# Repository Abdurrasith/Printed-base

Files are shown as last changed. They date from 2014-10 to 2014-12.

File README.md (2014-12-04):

# Robopoly demonstration robot 3D printed base

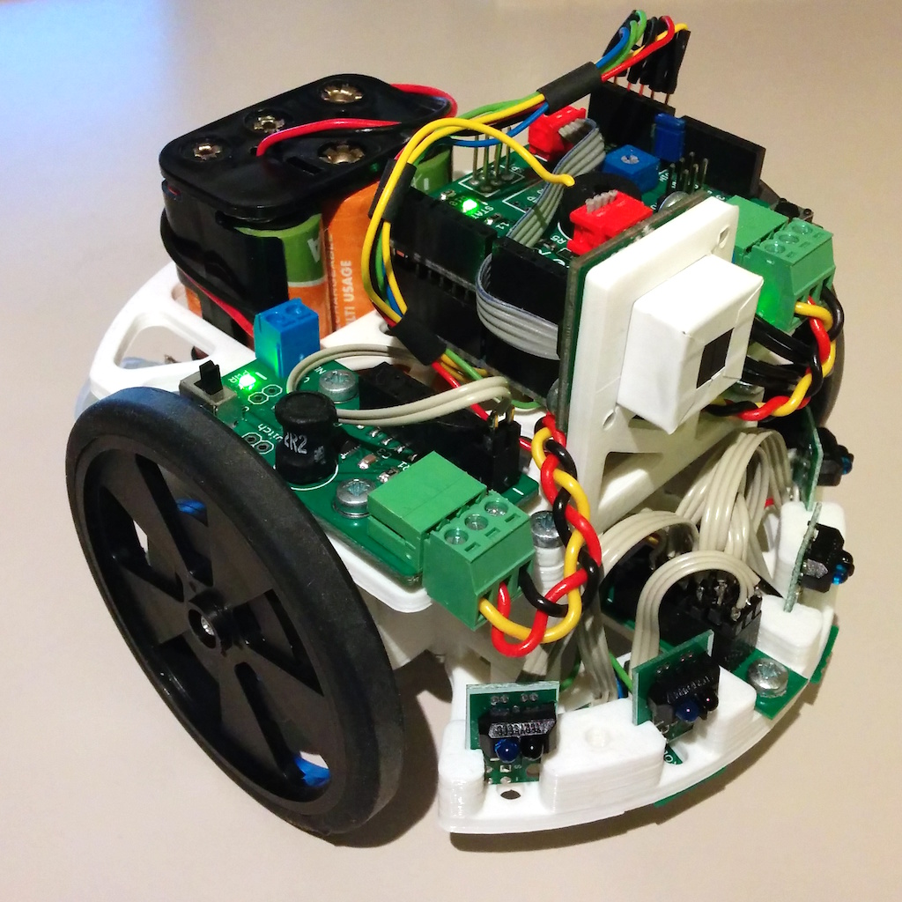
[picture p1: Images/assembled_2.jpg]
Demonstration robot front

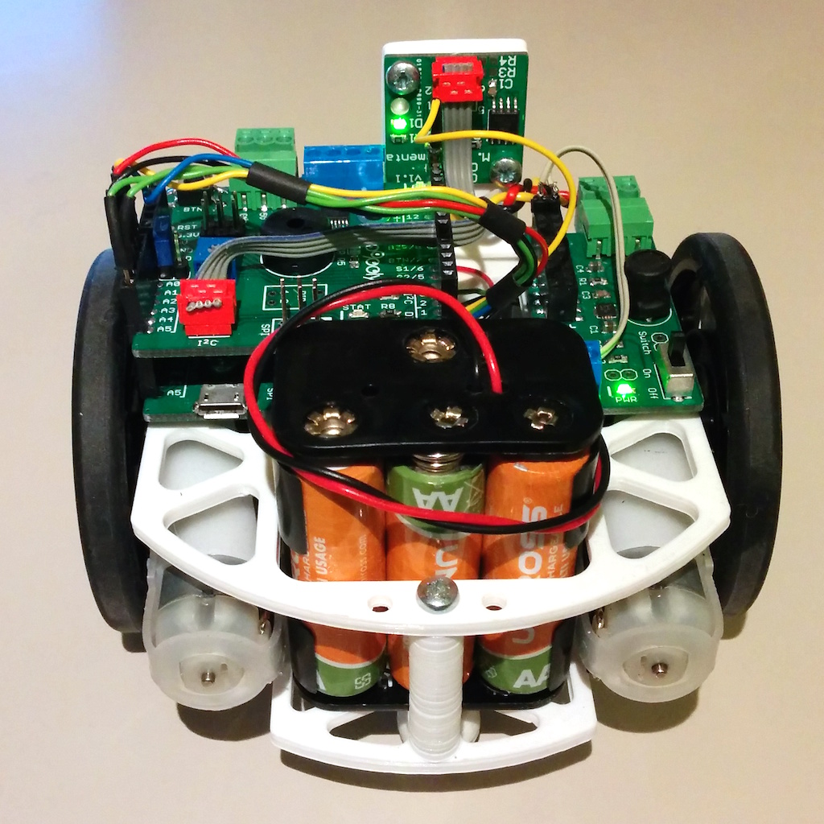
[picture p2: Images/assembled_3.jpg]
Demonstration robot back

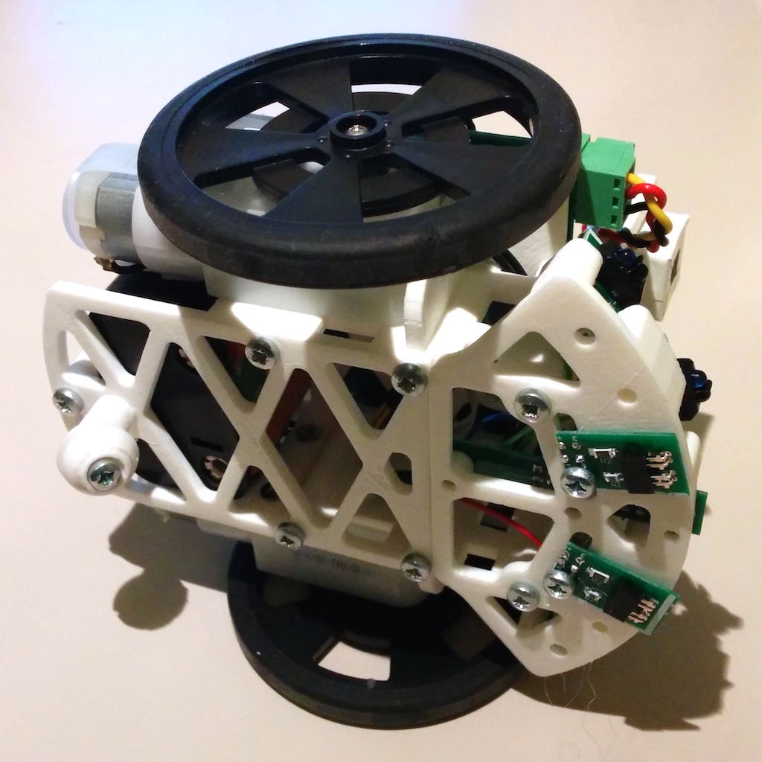
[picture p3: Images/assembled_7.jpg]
Printed caster wheel


The Robopoly demonstration robot is intended to serve as a modular base for demonstrations during [Robopoly lectures](http://robopoly.epfl.ch/demons) to show off the robotics platform capabilities. It is modular, all important parts are accessible, has a small footprint and is made only using electronics from the [kit PRisme](http://robopoly.epfl.ch/prisme).

## Design

Since the parts are intended to be printed with a 3D printer with fused filament fabrication (FFF) method they are small and full of holes in order to avoid warp because of uneven material cooling on 3D printers lacking a heated bed and using excessive amounts of material.

The front of the robot can accomodate different modules depending on the task at hand. 4 holes for M3 screws can be used to attach a custom add-on.

The center of the platform is empty, that space can be used to route electrical wires from the front of the robot to the [PRismino](https://github.com/Robopoly/PRismino) or store some additional electronics.

The USB port is easely accessible for programming and all the electronics are on top of the robot allowing easy access.

Horizontal holes in the supports are square because when printing big horizontal round holes with FFF method the plastic tends to warp upwards when the hole is being closed at the top because of unequal cooling, this basically creates an obstacle for the extruder which is to be avoided at all costs, square holes do not warp.

## Parts list

| Part | Quantity |
| --- | --- |
| Base | 1 |
| Top | 1 |
| Support left | 1 |
| Support right | 1 |
| Support rear | 1 |
| Caster roller | 1 |
| Caster wheel | 1 |
| Front | 1 |
| Linear camera support | 1 |
| M3x8 countersunk head screw for motors | 4 |
| M3x5 pan head screw for rear support | 2 |
| M3x8 pan head screw for electronics, rear support and caster roller | 5 |
| M3x10 countersunk head screw for caster wheel | 1 |
| M3x10 pan head screw for the frame | 10 |
| M3 washer for caster roller | 1 |

When assembling start with the motors as the holes won't be accessible with a screwdriver later on.

## Robopoly Control Center

The plaform is suited to be used with [Robopoly Control Center](https://github.com/Robopoly/RobopolyControlCenter), a [Google Chrome add-on](https://chrome.google.com/webstore/detail/robopoly-control-center/kimabfnmacaikklmibbbomomjffkfalo) that can remotely control the mobile platform, make it do some tasks and report pin values over USB or Bluetooth.

## Licence

The Robopoly demonstration robot printed base is published under [Creative Commons Attribution license](http://creativecommons.org/licenses/by/3.0/).



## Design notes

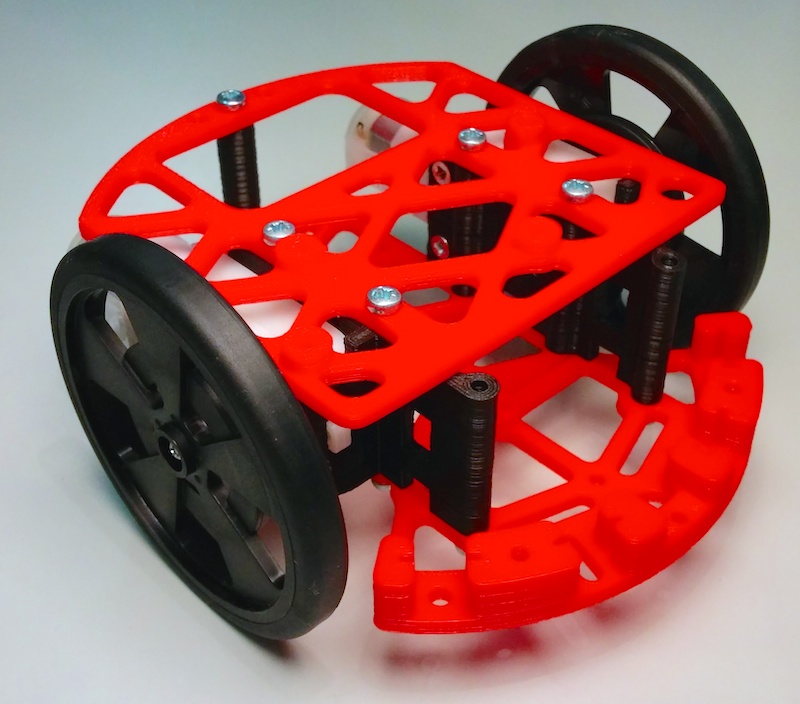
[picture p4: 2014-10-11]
Images/demo_1.jpg

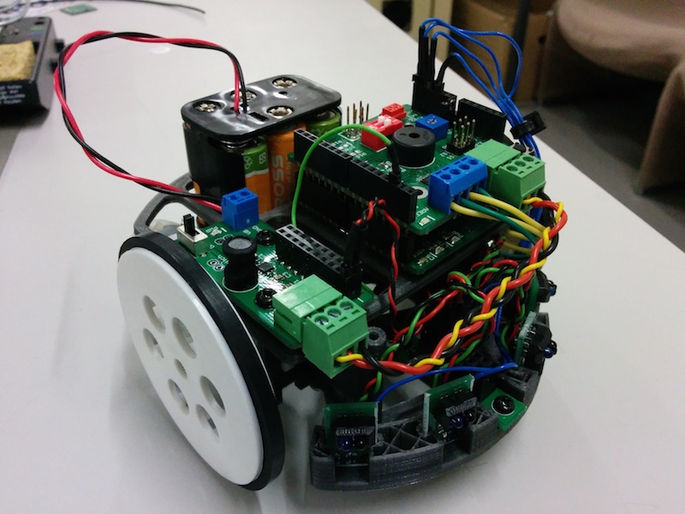
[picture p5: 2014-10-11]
Images/prototype.jpg

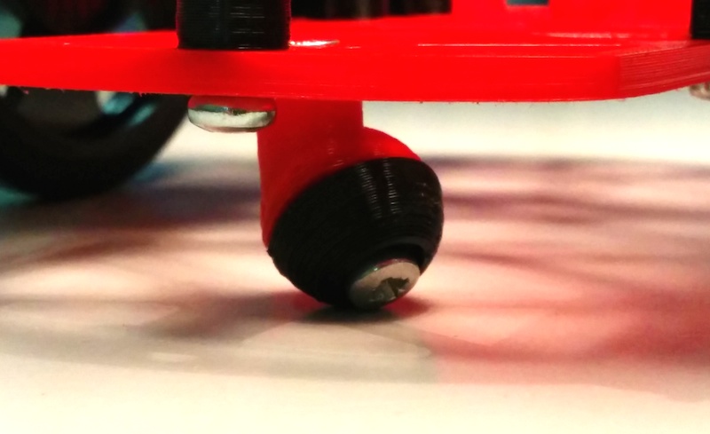
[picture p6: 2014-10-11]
Images/demo_3.jpg

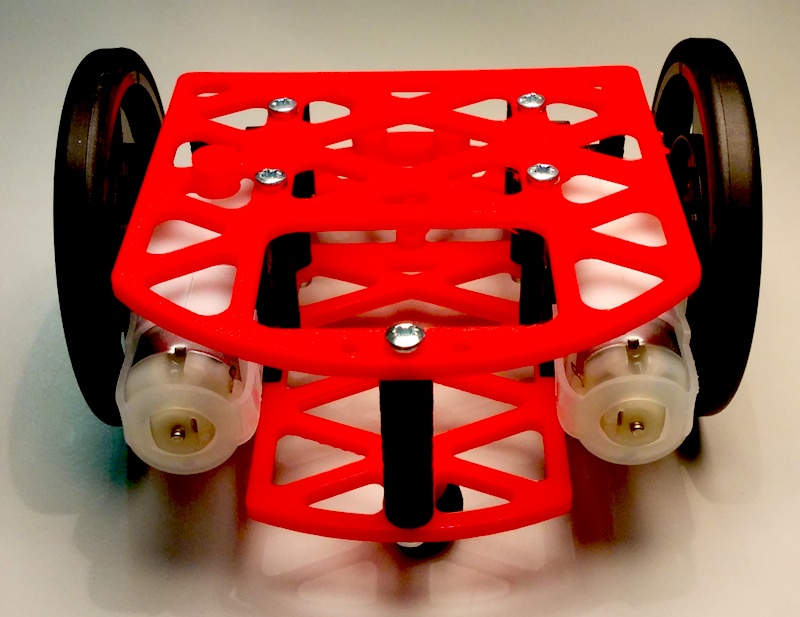
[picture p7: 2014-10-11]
Images/demo_2.jpg

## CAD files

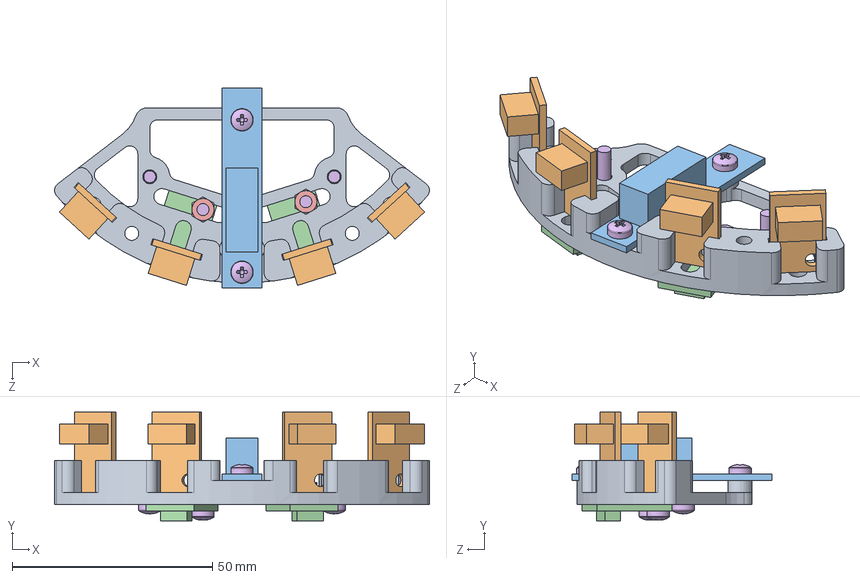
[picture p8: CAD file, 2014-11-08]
SolidWorks files/front_assembly.SLDASM
93.5 x 27.1 x 50.0 mm
front
ir_tcrt5000 x 4
rack
ir_tcrt1000 x 2
hex nut style 1 gradeab_iso x 2
pan head cross recess screw_iso x 6

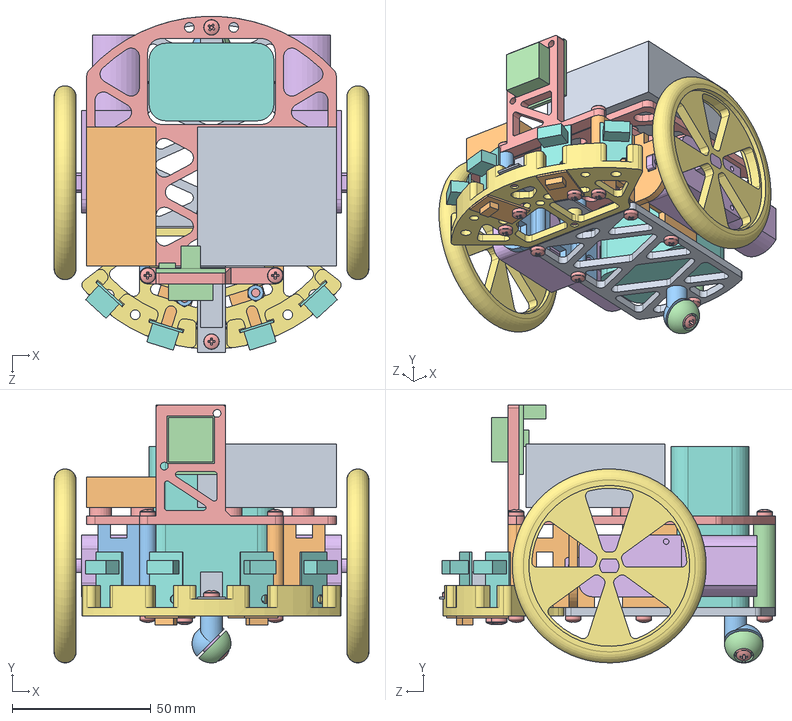
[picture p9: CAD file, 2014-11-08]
SolidWorks files/assembly.SLDASM
113.6 x 93.0 x 121.3 mm
base
support_left
support_right
support_rear
top
motor x 2
wheel x 2
battery_pack
prismino
power
caster_wheel
caster_roller
pan head cross recess screw_iso x 23
plain washer 10669 type nl_iso
front
ir_tcrt5000 x 4
rack
ir_tcrt1000 x 2
hex nut style 1 gradeab_iso x 2
linear_camera
support_linear_camera
countersunk flat head cross recess screw_iso x 5

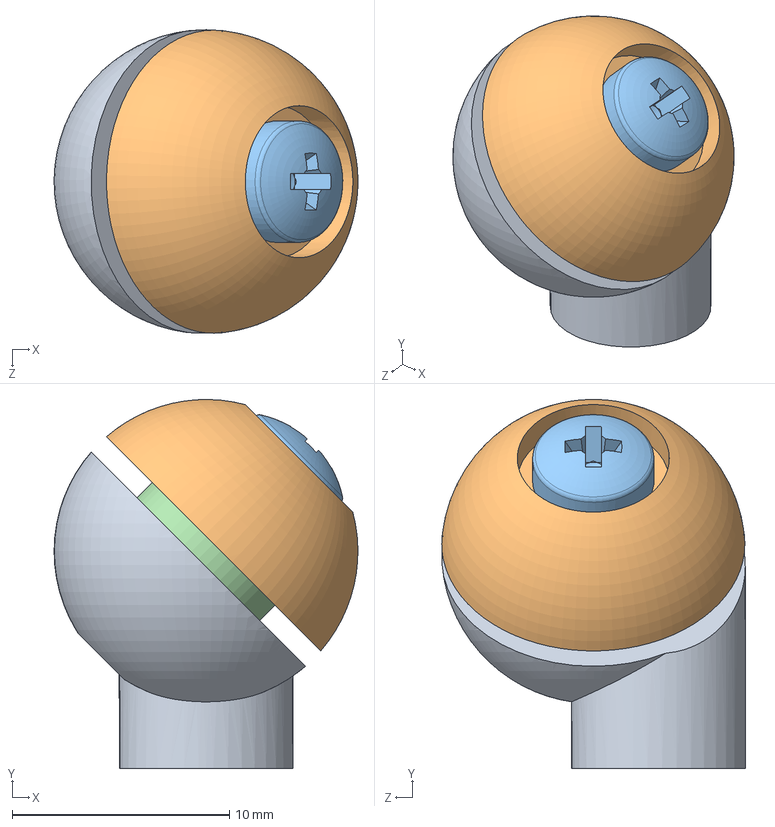
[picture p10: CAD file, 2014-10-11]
SolidWorks files/caster_assembly.SLDASM
14.0 x 17.0 x 14.0 mm
caster_wheel
caster_roller
pan head cross recess screw_iso
plain washer 10669 type nl_iso

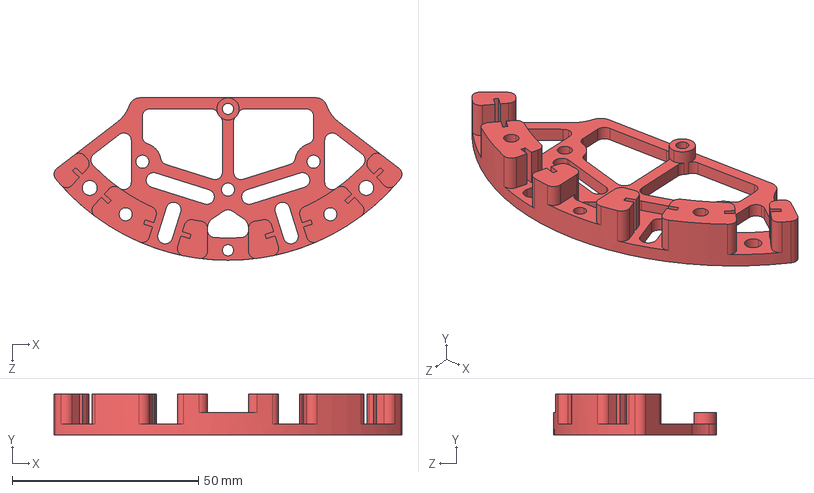
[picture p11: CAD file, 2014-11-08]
STEP files/front.STEP
93.5 x 11.0 x 43.7 mm

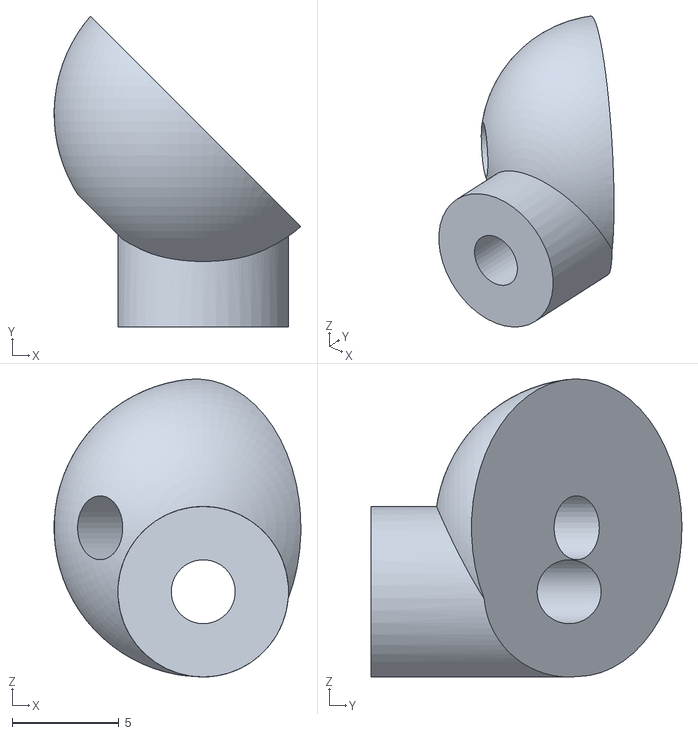
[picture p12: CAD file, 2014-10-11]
STL files/caster_base.STL
11.6 x 14.6 x 14.0

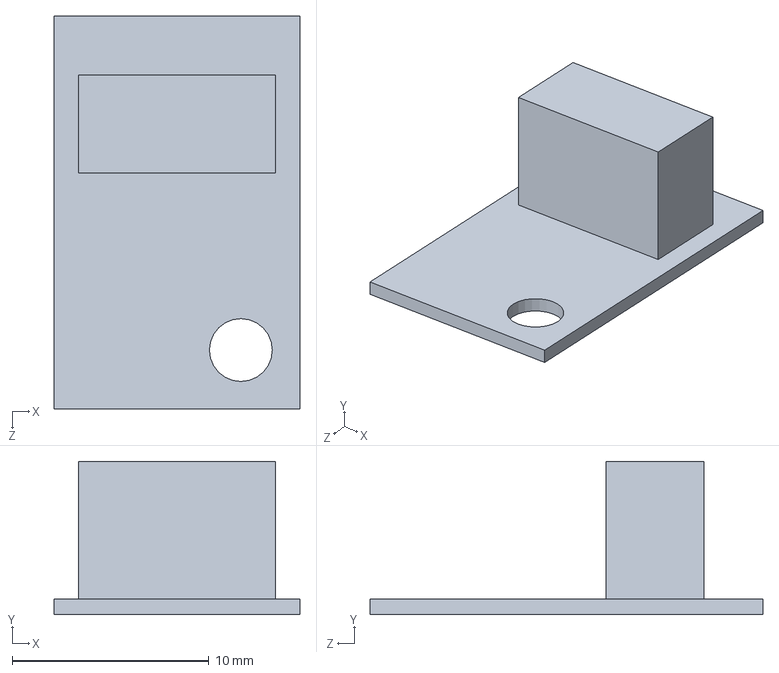
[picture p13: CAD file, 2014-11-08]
SolidWorks files/ir_tcrt5000.SLDPRT
12.5 x 7.80 x 20.0 mm

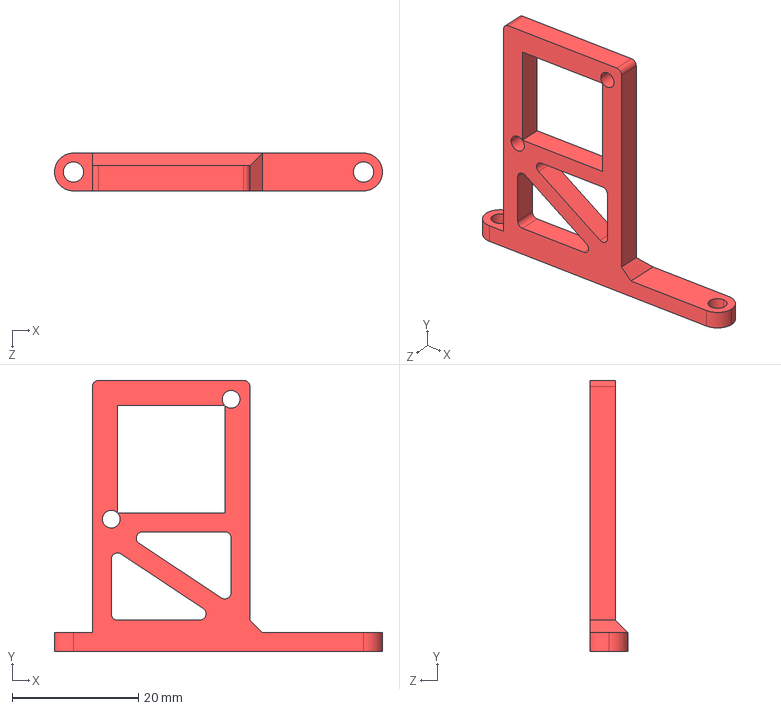
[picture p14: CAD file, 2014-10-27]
STEP files/support_linear_camera.STEP
52.0 x 43.0 x 6.00 mm

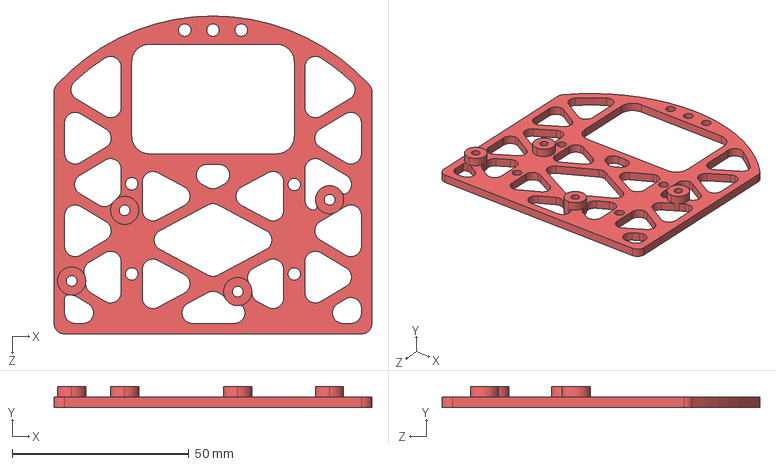
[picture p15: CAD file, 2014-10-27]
STEP files/top.STEP
90.0 x 6.00 x 90.0 mm

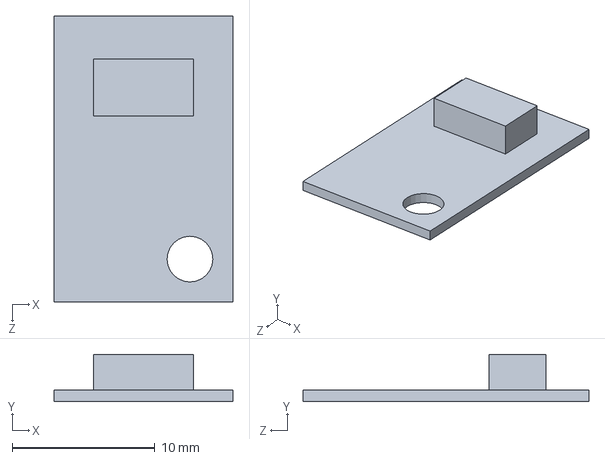
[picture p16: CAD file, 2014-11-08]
SolidWorks files/ir_tcrt1000.SLDPRT
12.5 x 3.30 x 20.0 mm

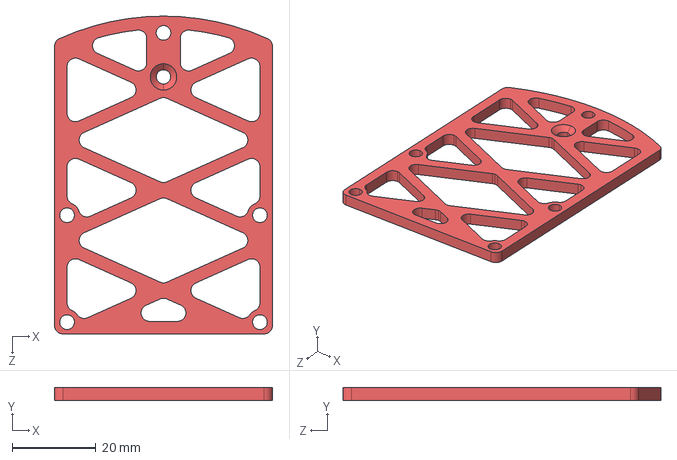
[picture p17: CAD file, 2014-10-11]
STEP files/base.STEP
52.0 x 3.00 x 75.8 mm

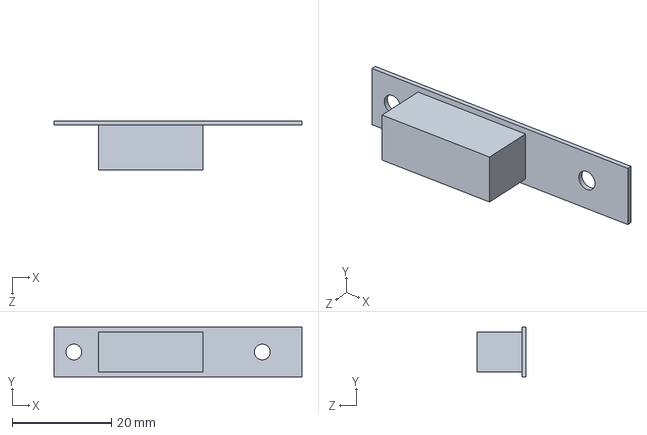
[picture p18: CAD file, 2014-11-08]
SolidWorks files/rack.SLDPRT
50.0 x 10.0 x 9.80 mm

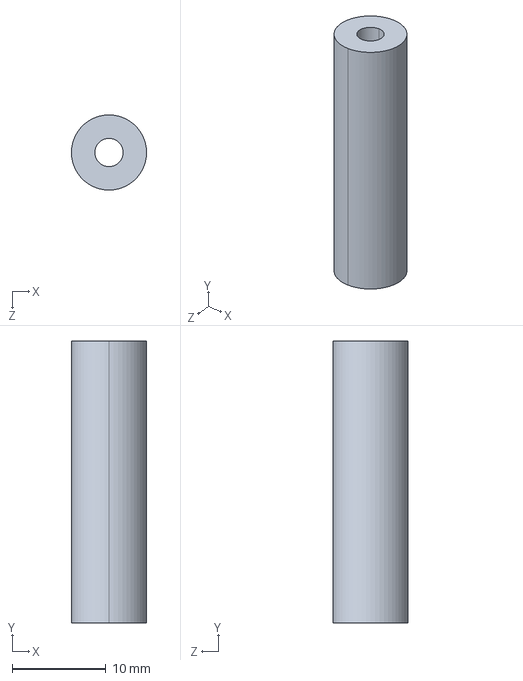
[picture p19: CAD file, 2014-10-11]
STEP files/support_rear.STEP
8.00 x 30.0 x 8.00 mm

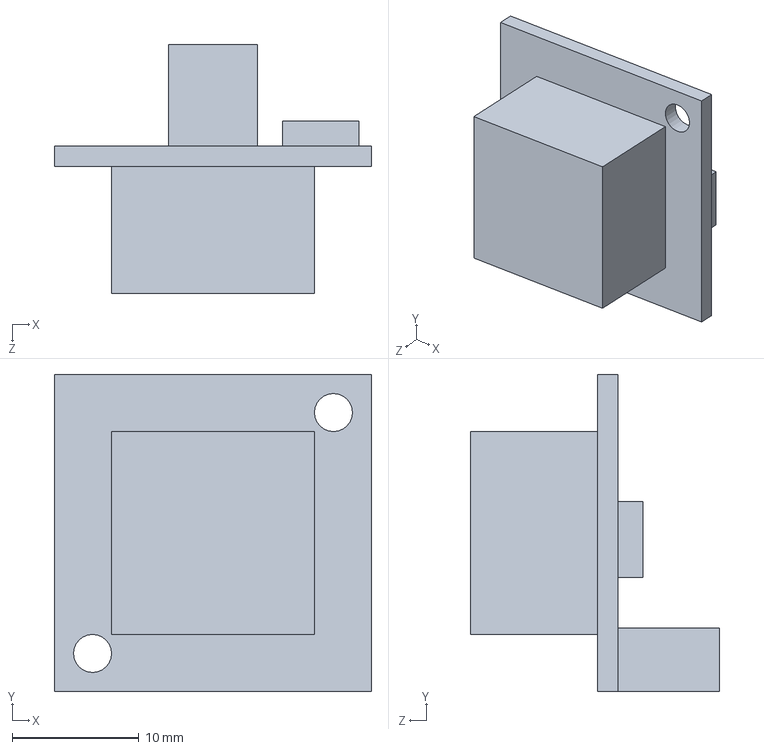
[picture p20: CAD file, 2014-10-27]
SolidWorks files/linear_camera.SLDPRT
25.0 x 25.0 x 19.6 mm

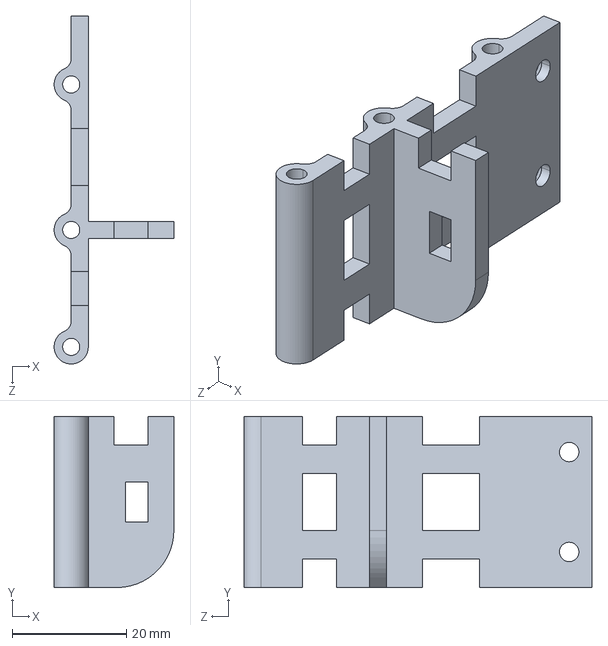
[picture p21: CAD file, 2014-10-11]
STEP files/support_left.STEP
21.0 x 30.0 x 61.0 mm

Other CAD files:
SolidWorks files/wheel.SLDPRT
STEP files/caster_roller.STEP
SolidWorks files/battery_pack.SLDPRT
STEP files/support_right.STEP
STEP files/caster_wheel.STEP
STL files/base.STL
STL files/caster_roller.STL
STL files/front.STL
STL files/support_left.STL
STL files/support_linear_camera.STL
STL files/support_rear.STL
STL files/support_right.STL
STL files/top.STL
SolidWorks files/base.SLDPRT
SolidWorks files/caster_roller.SLDPRT
SolidWorks files/caster_wheel.SLDPRT
SolidWorks files/front.SLDPRT
SolidWorks files/motor.SLDPRT
SolidWorks files/power.SLDPRT
SolidWorks files/support_left.SLDPRT
SolidWorks files/support_linear_camera.SLDPRT
SolidWorks files/support_rear.SLDPRT
SolidWorks files/support_right.SLDPRT
SolidWorks files/top.SLDPRT

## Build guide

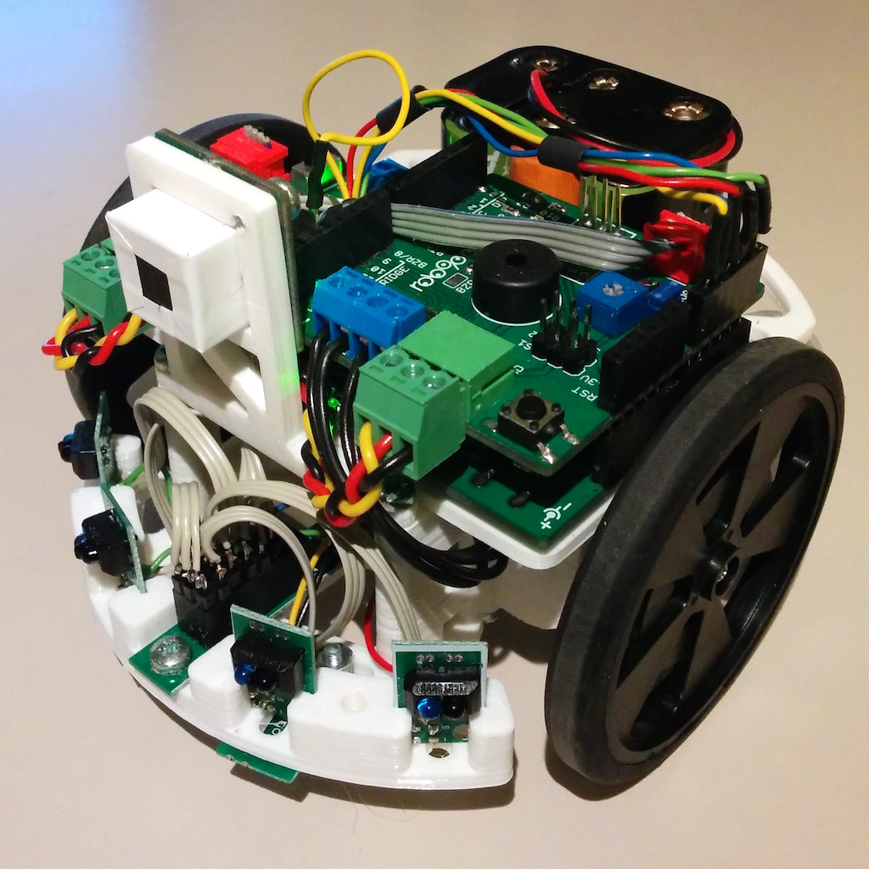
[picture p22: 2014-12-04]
Images/assembled_1.jpg

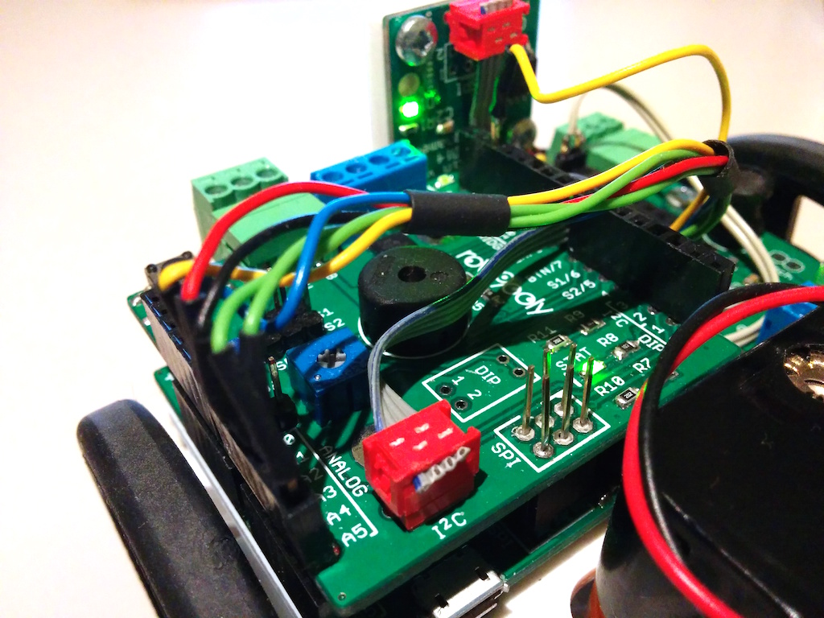
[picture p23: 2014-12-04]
Images/assembled_6.jpg

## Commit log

2014-10-27 Made battery compartment bigger, added linear camera support
    The battery compartment was too small and damaged the batteries when
    they were inserted.
    [assembly.SLDASM, front_assembly.SLDASM, linear_camera.SLDPRT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]
2014-11-08 Modified front part to accommodate thinner IR sensor PCBs
    [assembly.SLDASM, front.SLDPRT, front.STEP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]
